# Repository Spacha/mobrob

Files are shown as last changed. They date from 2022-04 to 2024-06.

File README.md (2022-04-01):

# mobrob

A mobile robot 

## Features

* Obstacle detection and avoidance
* Room mapping (explore mode?)
* Manual control (throttle + steer)
  * For example, through browser-based GUI
* Automatic navigation (A to B) (after exploring space?)
  * Complete more complex tasks like _fetch an item_?
* Charging capability preferable (e.g. MCP73831)
  * https://www.youtube.com/watch?v=GRd9uTwg7r4&ab_channel=MicroTypeEngineering
  * https://www.youtube.com/watch?v=TyaW8ZKumno&ab_channel=PlumPot

# Initial design

Datasheets for components are found in `Datasheets` folder.

* **Processor & connectivity**: ESP8266 | [datasheet](datasheets/ESP8266EX_datasheet-v4.4.pdf)
  * These values are for ESP8266EX
  * WiFi: 802.11 b/g/n Wifi, 2.4-2.5 GHz
  * Peripherals: UART / SDIO / SPI / I2C / I2S / IR Remote Control / GPIO / PWM
  * Operating voltage 3.3V (3.0-3.6V)
  * Average operating current: 80 mA
  * Around 50 kB RAM (for user, when connected to a station)
  * **Requires external SPI flash!** Up to 16 MB flash can be supported
    * Suggested: 512 kB (without OTA), 1 MB (with OTA)
  * Single core, 80 MHz
* **Dual H-bridge motor driver**: L293D | [datasheet](datasheets/L293x_datasheet.pdf)
* Power management:
  * **Battery**: 11.1V Li-Po (6-12V), (3 x 3.7V cells)
    * Price: $20-40
  * **Buck converter (12V->5V)**: LM2596 or other...
    * https://www.youtube.com/watch?v=C7-8nUU6e3E&t=2367s
  * **LDO (5V->3.3V)**: LM7805
    * https://electronics.stackexchange.com/questions/420999/use-5v-linear-regulator-and-ldo-3-3v

* **Motors & chassis**: Dual motor tank chassis (3-7V)
  * https://www.aliexpress.com/item/4000115994387.html?spm=a2g0o.order_list.0.0.21ef1802jPbMxm
  * Has slot for 4xAA batteries, could be modified to fit the rechargable 3-cell Li-Po battery.
  * Size: 9.7cm x 18.5cm x 5cm (width x length x height )
  * Motors: 130 size generic, can be replaced if necessary
  * Price: $18.50

* Sensors (both for proximity and distance, and other):
  * IMU?
  * UT/IR?
  * Others?

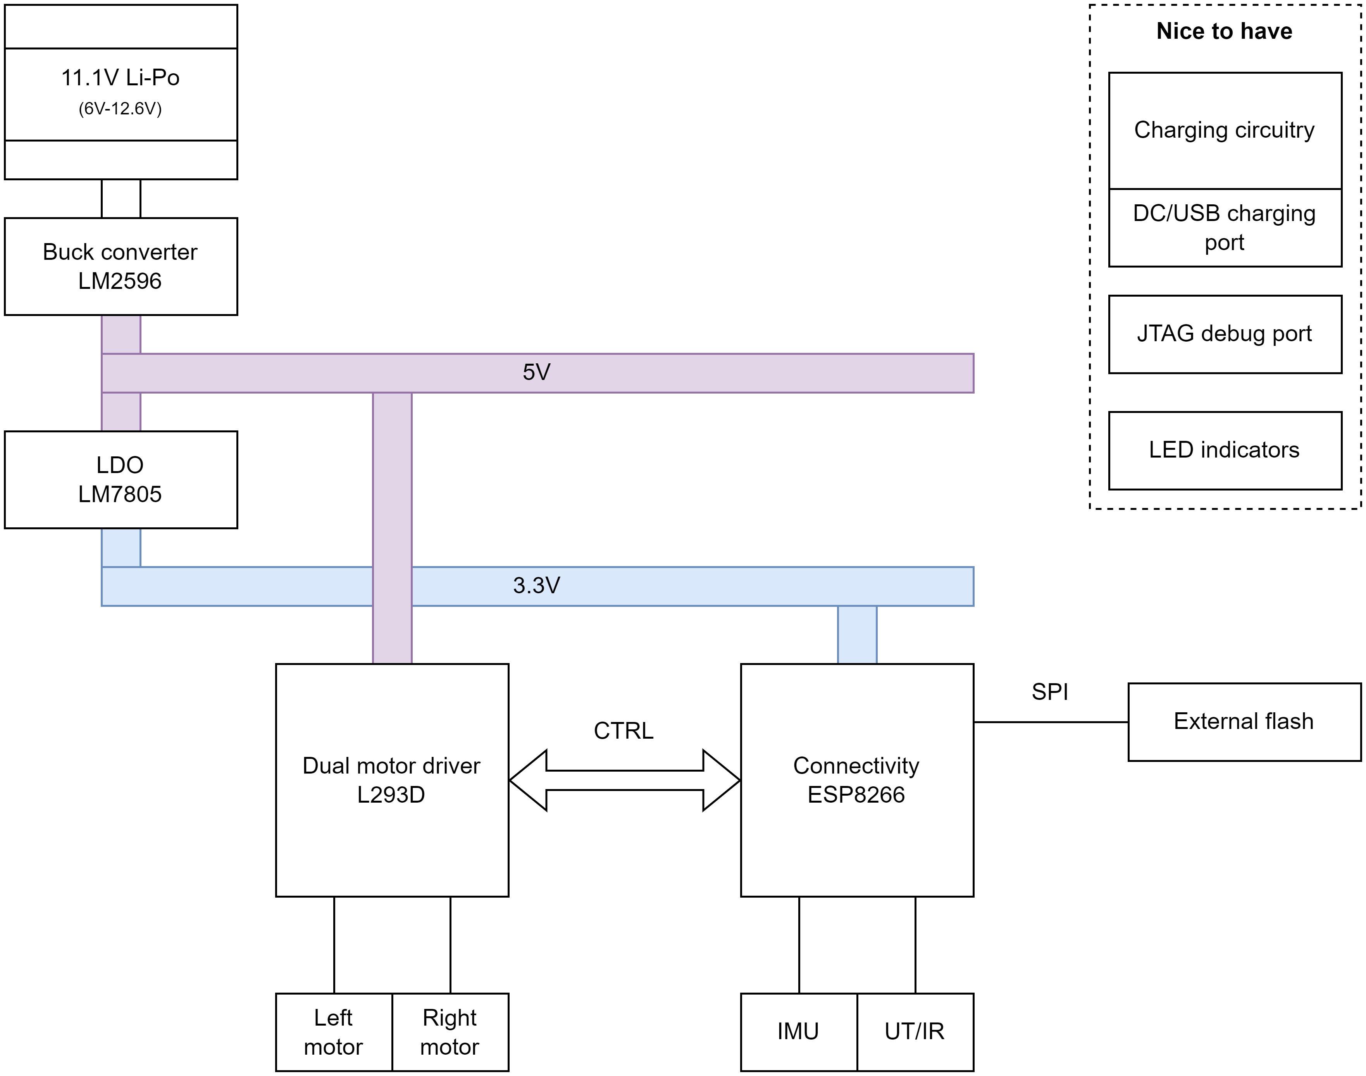
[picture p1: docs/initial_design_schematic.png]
Initial design.


# Discussion

I am not sure if either ESP32 or ESP8266 come in QFP format (only in QFN, no-leads). I guess JLCPCB and others also assemble these devices so maybe this is not an issue.

## ESP32
ESP32 would be considerably better than ESP8266. It has a lot more functionality and also has 8MB of onboard flash (ESP32-S3FN8, see ESP32-S3 datasheet, p.11).

* https://www.youtube.com/watch?v=WWIy6a0T7WM&ab_channel=PlumPot
* Decoupling caps (as close of the pins as possible)
* External crystal? (see Phil's lab)
* Note the antenna/RF part!
  * No traces (or any copper) beneath the antenna part!
* Careful with differential pairs

* https://en.wikipedia.org/wiki/ESP32#ESP32-S3:
  * ESP32-WROOM-32D: PCB trace antenna, 4 MiB flash (probably preferable)
  * ESP32-WROOM-32U: U.FL socket antenna, 4 MiB flash

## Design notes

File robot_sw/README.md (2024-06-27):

# Mobrob

In this project, a mobile robot with remote control capability is developed. The robot will be able to wirelessly connect to Wi-Fi and sense the obstacles in its environment. The robot will be able to receive commands from the remote server, and send sensor readings and other data back to the server.

The system can be used as a base for a robot-based home security system, an in-home sensor platform, or with some improvements, even for industrial applications, completing dull, dirty, and dangerous tasks.

Miika and Essi

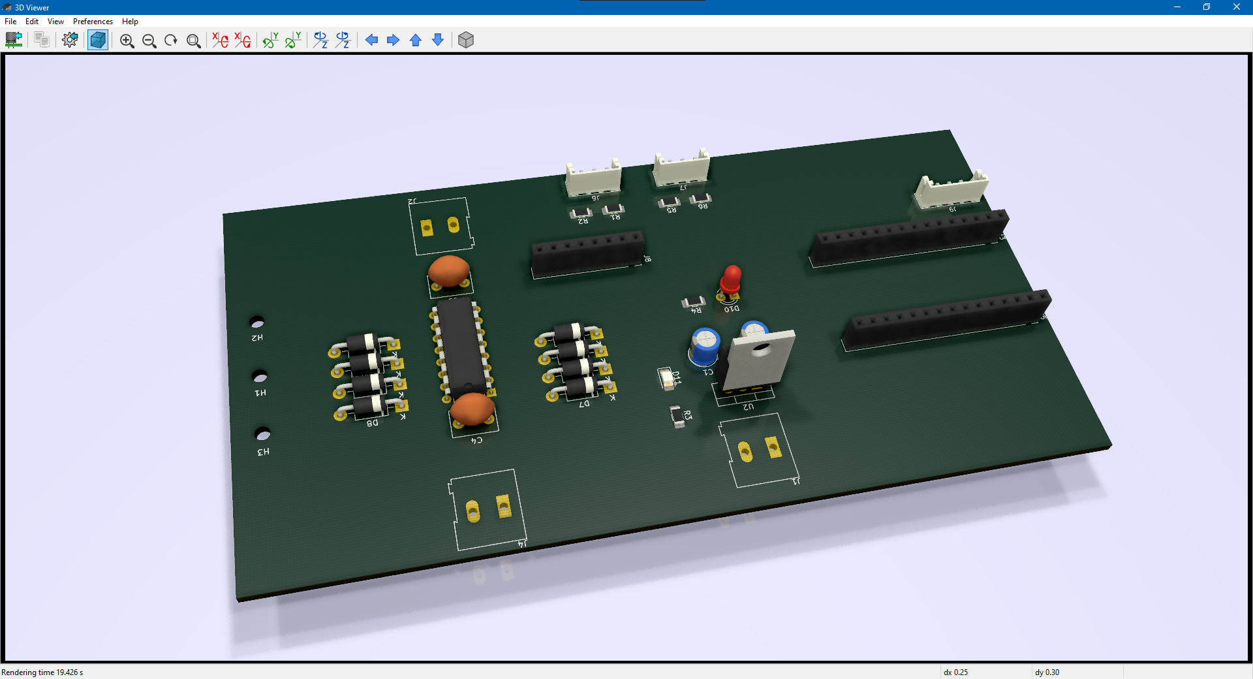
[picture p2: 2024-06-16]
Annotation 2024-05-02 180300.png

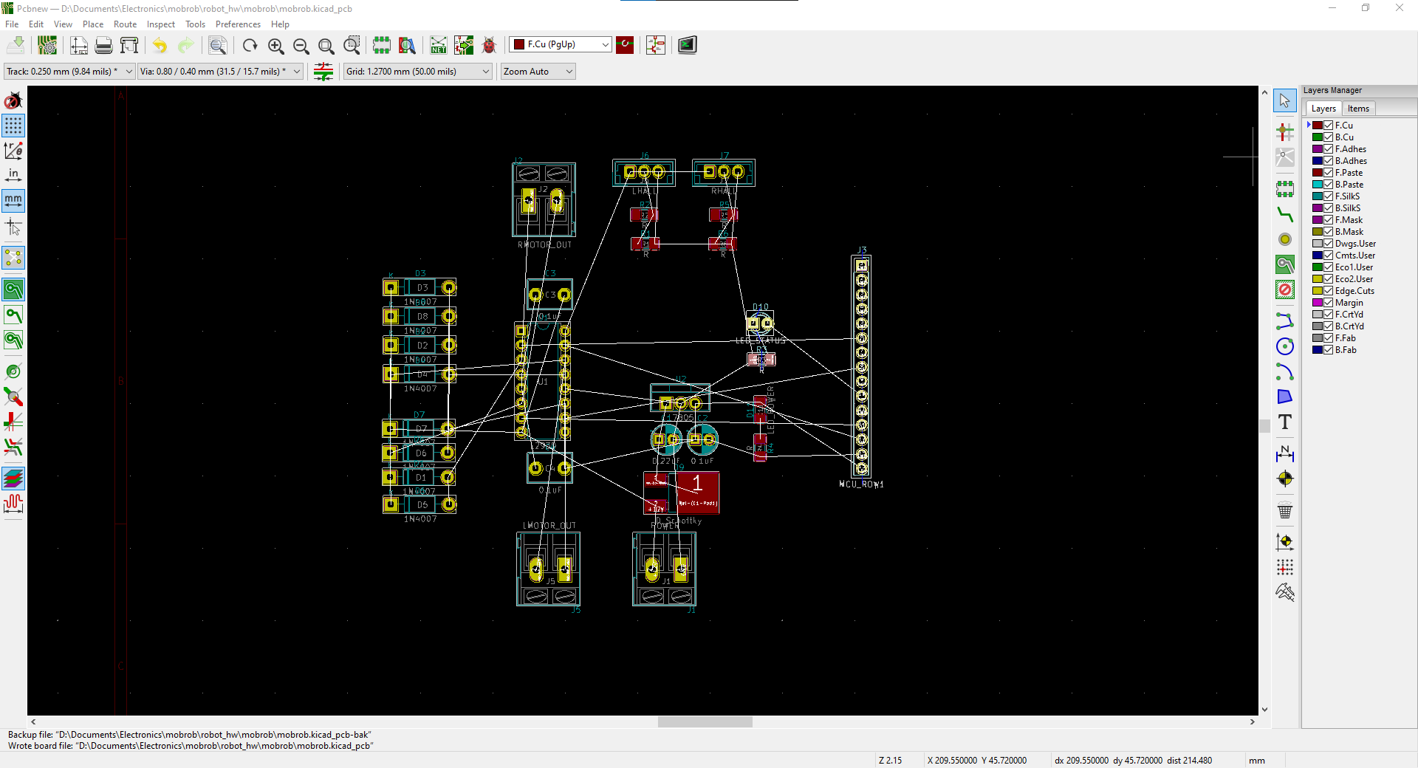
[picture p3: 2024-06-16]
Annotation 2024-04-15 024806.png

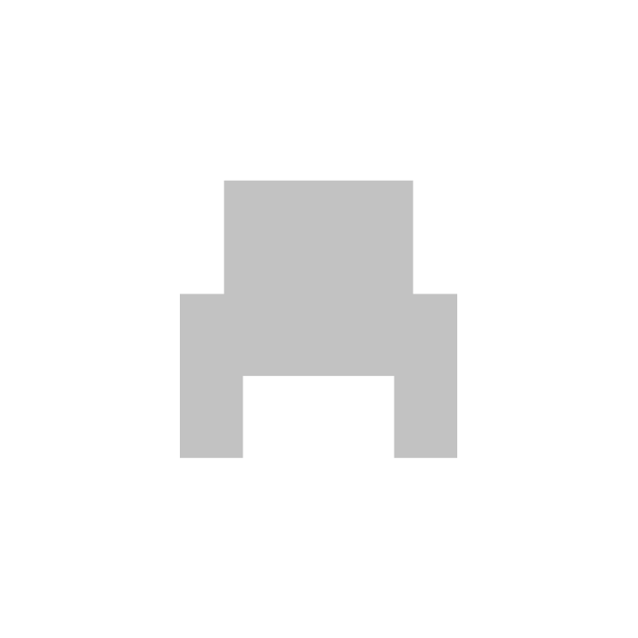
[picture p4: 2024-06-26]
server_sw/resources/view_rear.png

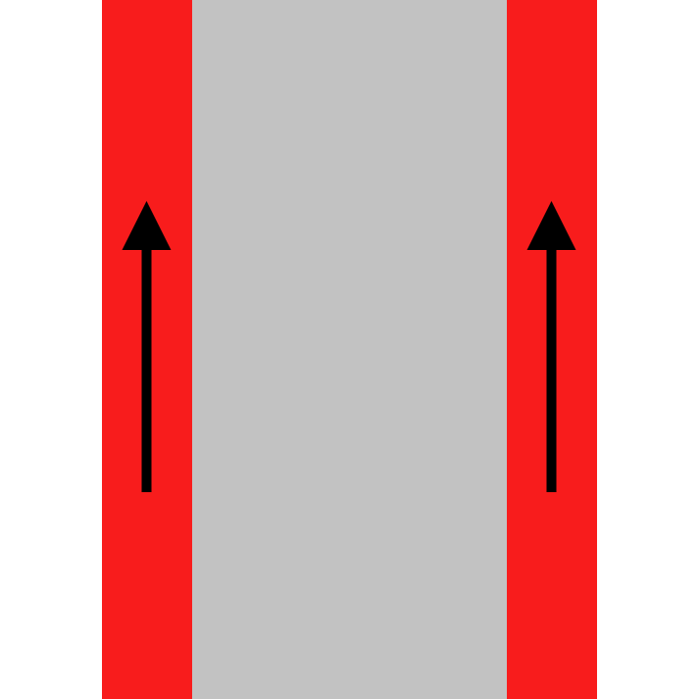
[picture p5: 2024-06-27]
server_sw/resources/view_top_lfrf.png

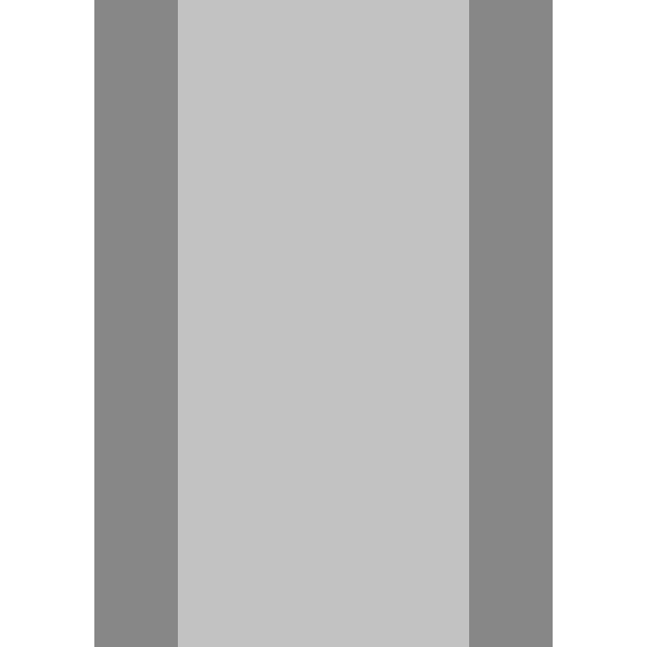
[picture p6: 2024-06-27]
server_sw/resources/view_top.png

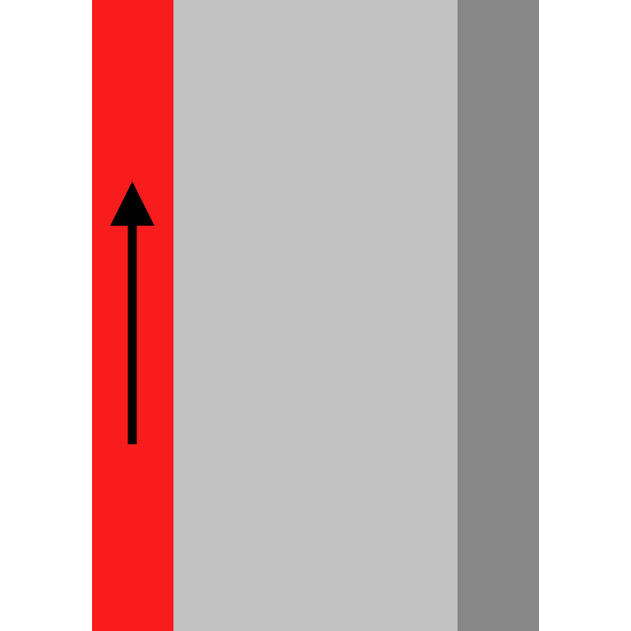
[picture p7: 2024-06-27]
server_sw/resources/view_top_lf.png

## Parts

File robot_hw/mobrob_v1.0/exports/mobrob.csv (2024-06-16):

Reference | Value | Datasheet | Footprint | Qty | DNP
C1 | 0.22uF | ~ | Capacitor_THT:CP_Radial_D10.0mm_P5.00mm | 1
C2,C3,C4 | 0.1uF | ~ | -- mixed values -- | 3
D1,D2,D3,D4,D5,D6,D7,D8 | M7 | https://diotec.com/request/datasheet/m1.pdf | Diode_SMD:D_SMA_Handsoldering | 8
D9 | LED_STATUS | http://cdn-reichelt.de/documents/datenblatt/A500/LL-504BC2E-009.pdf | LED_THT:LED_D5.0mm | 1
D10 | LED_POWER | https://optoelectronics.liteon.com/upload/download/DS-22-98-0004/LTST-C150GKT.pdf | LED_SMD:LED_1206_3216Metric_Pad1.42x1.75mm_HandSolder | 1
J1 | RMOTOR | https://www.on-shore.com/wp-content/uploads/ED555XDS.pdf | TerminalBlock_Phoenix:TerminalBlock_Phoenix_PT-1,5-2-3.5-H_1x02_P3.50mm_Horizontal | 1
J2 | LMOTOR | https://www.on-shore.com/wp-content/uploads/ED555XDS.pdf | TerminalBlock_Phoenix:TerminalBlock_Phoenix_PT-1,5-2-3.5-H_1x02_P3.50mm_Horizontal | 1
J3 | POWER | https://www.on-shore.com/wp-content/uploads/ED555XDS.pdf | TerminalBlock_Phoenix:TerminalBlock_Phoenix_PT-1,5-2-3.5-H_1x02_P3.50mm_Horizontal | 1
J4 | ESP32_1 | ~ | Connector_PinSocket_2.54mm:PinSocket_1x15_P2.54mm_Vertical | 1
J5 | ESP32_2 | ~ | Connector_PinSocket_2.54mm:PinSocket_1x15_P2.54mm_Vertical | 1
J6,J7 | LHALL | ~ | Connector_PinHeader_2.54mm:PinHeader_1x03_P2.54mm_Vertical | 2
J8 | IMU | ~ | Connector_PinSocket_2.54mm:PinSocket_1x08_P2.54mm_Vertical | 1
J9 | UT | ~ | Connector_PinHeader_2.54mm:PinHeader_1x04_P2.54mm_Vertical | 1
R1,R2 | 150 | ~ | Resistor_SMD:R_0805_2012Metric_Pad1.20x1.40mm_HandSolder | 2
U1 | L293D | http://www.ti.com/lit/ds/symlink/l293.pdf | Package_DIP:DIP-16_W7.62mm | 1
U2 | L7805 | http://www.st.com/content/ccc/resource/technical/document/datasheet/41/4f/b3/b0/12/d4/47/88/CD00000444.pdf/files/CD00000444.pdf/jcr:content/translations/en.CD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 | Package_TO_SOT_THT:TO-220-3_Vertical | 1

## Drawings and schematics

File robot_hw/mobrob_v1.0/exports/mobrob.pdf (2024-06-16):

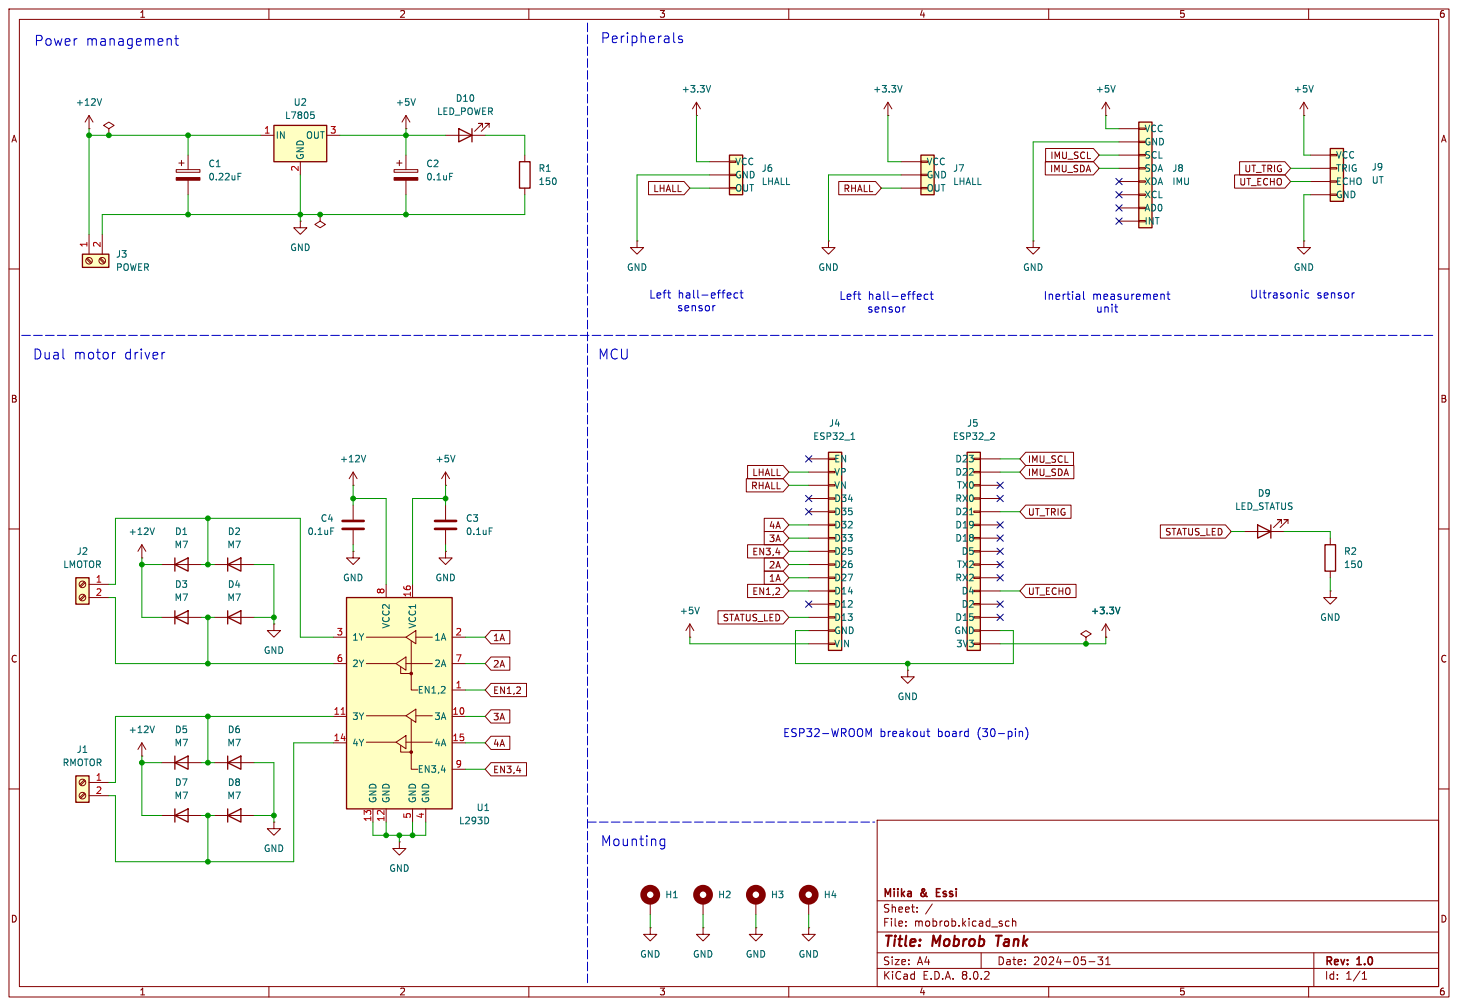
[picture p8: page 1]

Left hall-effect sensor ESP32-WROOM breakout board (30-pin)

Id: 1/1 Title: Mobrob Tank

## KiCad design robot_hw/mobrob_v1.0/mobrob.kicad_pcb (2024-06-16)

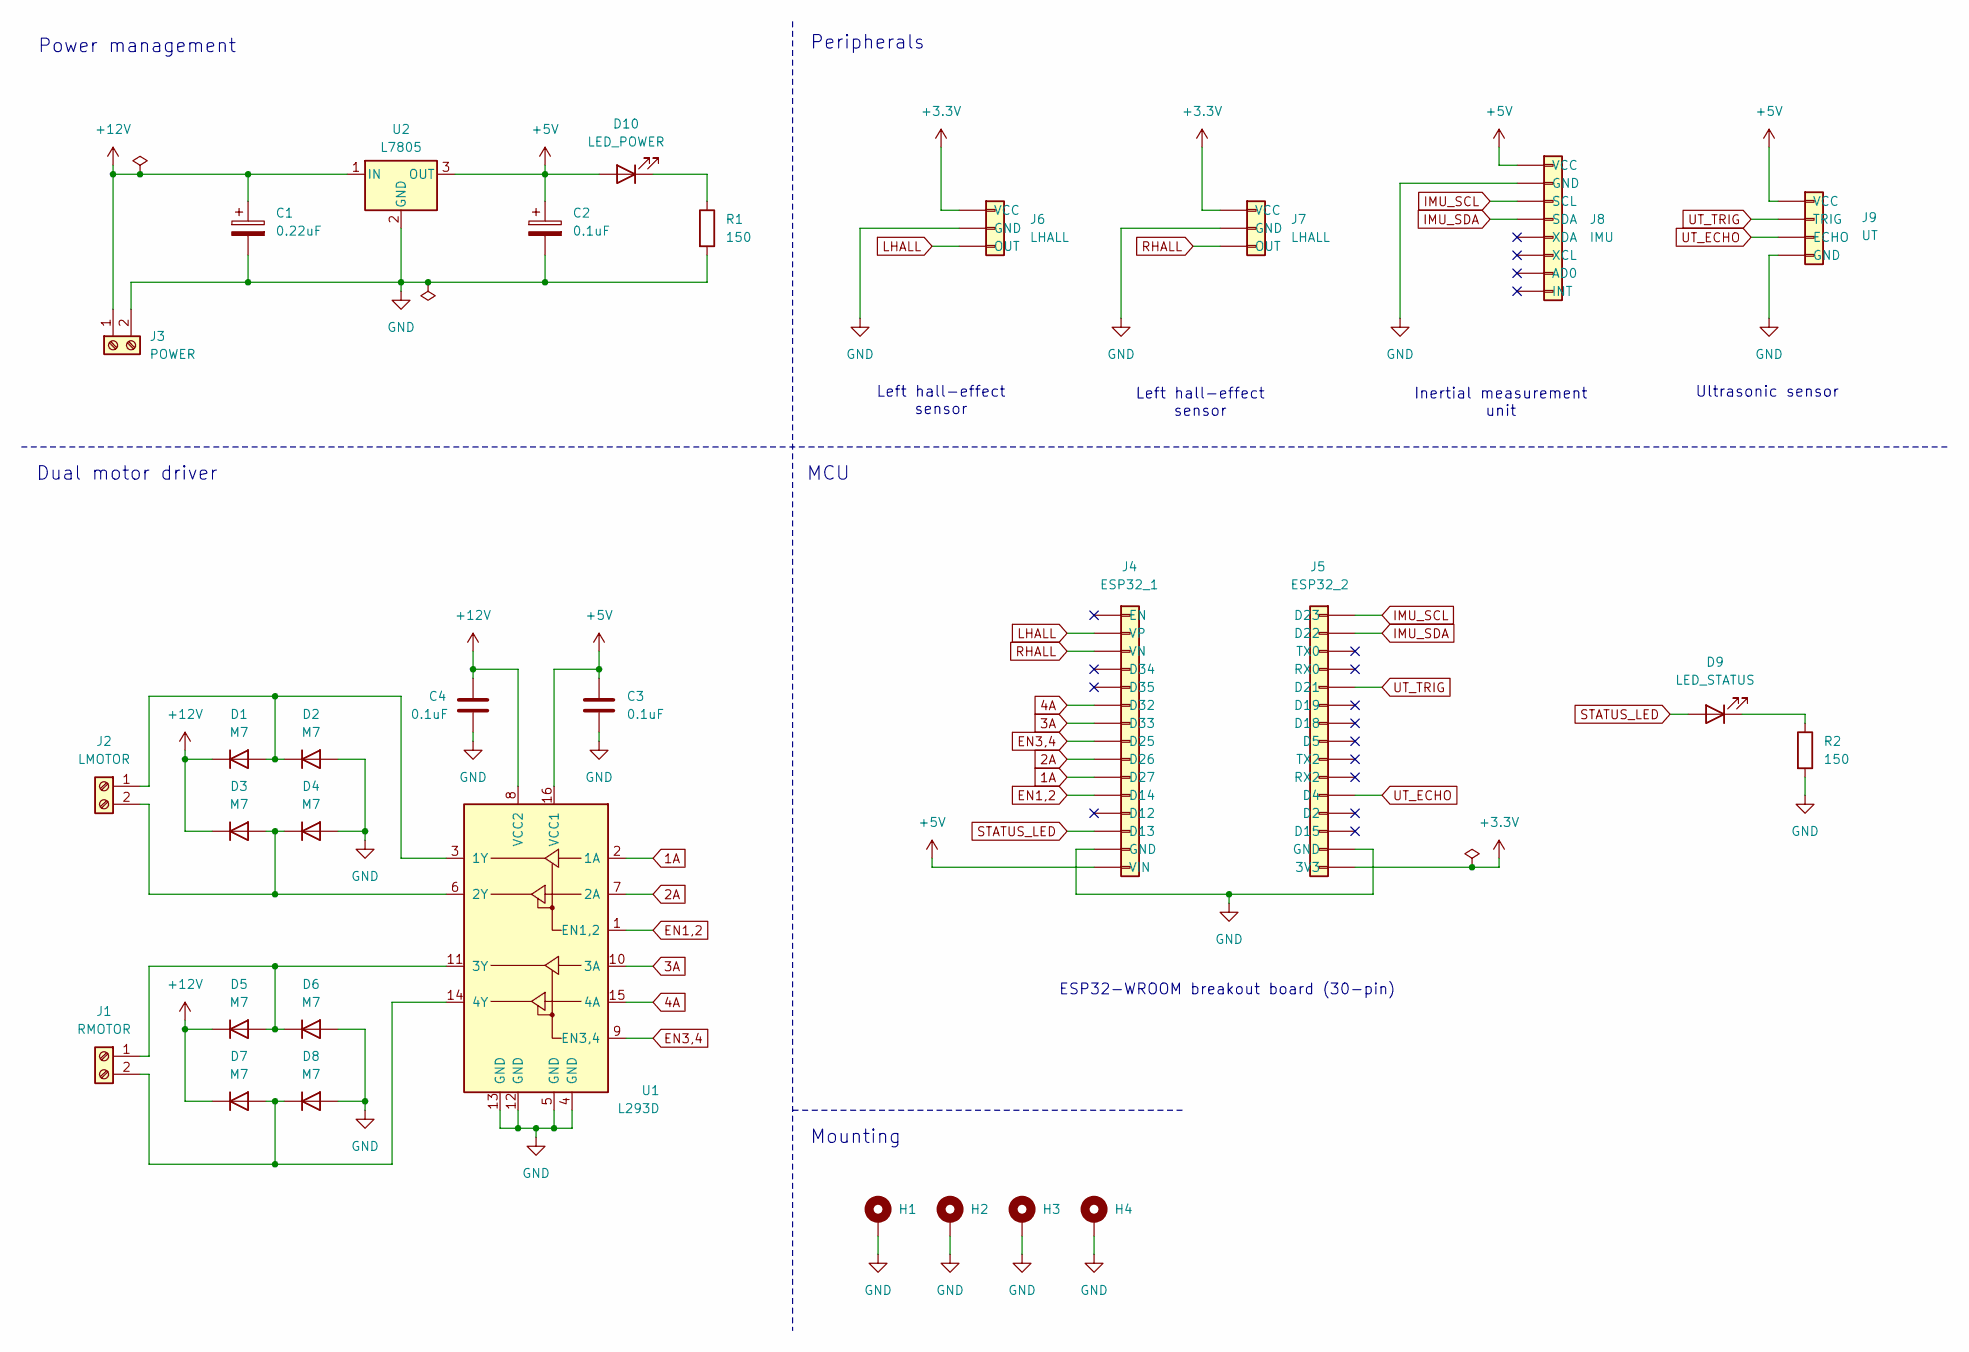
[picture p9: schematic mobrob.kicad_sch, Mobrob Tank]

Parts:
C1: 0.22uF; CP_Radial_D10.0mm_P5.00mm
C2: 0.1uF; CP_Radial_D10.0mm_P5.00mm
C3, C4: 0.1uF; C_1206_3216Metric_Pad1.33x1.80mm_HandSolder
D1, D2, D3, D4, D5, D6, D7, D8: M7; D_SMA_Handsoldering
D9: LED_STATUS; LED_D5.0mm
D10: LED_POWER; LED_1206_3216Metric_Pad1.42x1.75mm_HandSolder
H1, H2, H3, H4: MountingHole_Pad; MountingHole_3.2mm_M3_Pad_Via
J1: RMOTOR; TerminalBlock_Phoenix_PT-1,5-2-3.5-H_1x02_P3.50mm_Horizontal
J2: LMOTOR; TerminalBlock_Phoenix_PT-1,5-2-3.5-H_1x02_P3.50mm_Horizontal
J3: POWER; TerminalBlock_Phoenix_PT-1,5-2-3.5-H_1x02_P3.50mm_Horizontal
J4: ESP32_1; PinSocket_1x15_P2.54mm_Vertical
J5: ESP32_2; PinSocket_1x15_P2.54mm_Vertical
J6, J7: LHALL; PinHeader_1x03_P2.54mm_Vertical
J8: IMU; PinSocket_1x08_P2.54mm_Vertical
J9: UT; PinHeader_1x04_P2.54mm_Vertical
R1, R2: 150; R_0805_2012Metric_Pad1.20x1.40mm_HandSolder
U1: L293D; DIP-16_W7.62mm
U2: L7805; TO-220-3_Vertical

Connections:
1A: J4.10 (D27), U1.2 (1A)
2A: J4.9 (D26), U1.7 (2A)
3A: J4.7 (D33), U1.10 (3A)
4A: J4.6 (D32), U1.15 (4A)
+3.3V: J5.15 (3V3), J6.1 (VCC), J7.1 (VCC)
+5V: C2.1, C3.1, D10.2 (A), J4.15 (VIN), J8.1 (VCC), J9.1 (VCC), U1.16 (VCC1), U2.3 (OUT)
+12V: C1.1, C4.1, D1.1 (K), D3.1 (K), D5.1 (K), D7.1 (K), J3.1, U1.8 (VCC2), U2.1 (IN)
EN1,2: J4.11 (D14), U1.1 (EN1,2)
EN3,4: J4.8 (D25), U1.9 (EN3,4)
GND: C1.2, C2.2, C3.2, C4.2, D2.2 (A), D4.2 (A), D6.2 (A), D8.2 (A), H1.1, H2.1, H3.1, H4.1, J3.2, J4.14 (GND), J5.14 (GND), J6.2 (GND), J7.2 (GND), J8.2 (GND), J9.4 (GND), R1.2, R2.2, U1.4 (GND), U1.5 (GND), U1.12 (GND), U1.13 (GND), U2.2 (GND)
IMU_SCL: J5.1 (D23), J8.3 (SCL)
IMU_SDA: J5.2 (D22), J8.4 (SDA)
LHALL: J4.2 (VP), J6.3 (OUT)
unnamed: D1.2 (A), D2.1 (K), J2.1, U1.3 (1Y)
unnamed: D3.2 (A), D4.1 (K), J2.2, U1.6 (2Y)
unnamed: D5.2 (A), D6.1 (K), J1.1, U1.11 (3Y)
unnamed: D7.2 (A), D8.1 (K), J1.2, U1.14 (4Y)
unnamed: D9.1 (K), R2.1
unnamed: D10.1 (K), R1.1
RHALL: J4.3 (VN), J7.3 (OUT)
STATUS_LED: D9.2 (A), J4.13 (D13)
UT_ECHO: J5.11 (D4), J9.3 (ECHO)
UT_TRIG: J5.5 (D21), J9.2 (TRIG)

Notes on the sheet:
Power management
Dual motor driver
MCU
Left hall-effect sensor
Mounting
ESP32-WROOM breakout board (30-pin)
Inertial measurement unit
Peripherals
Ultrasonic sensor

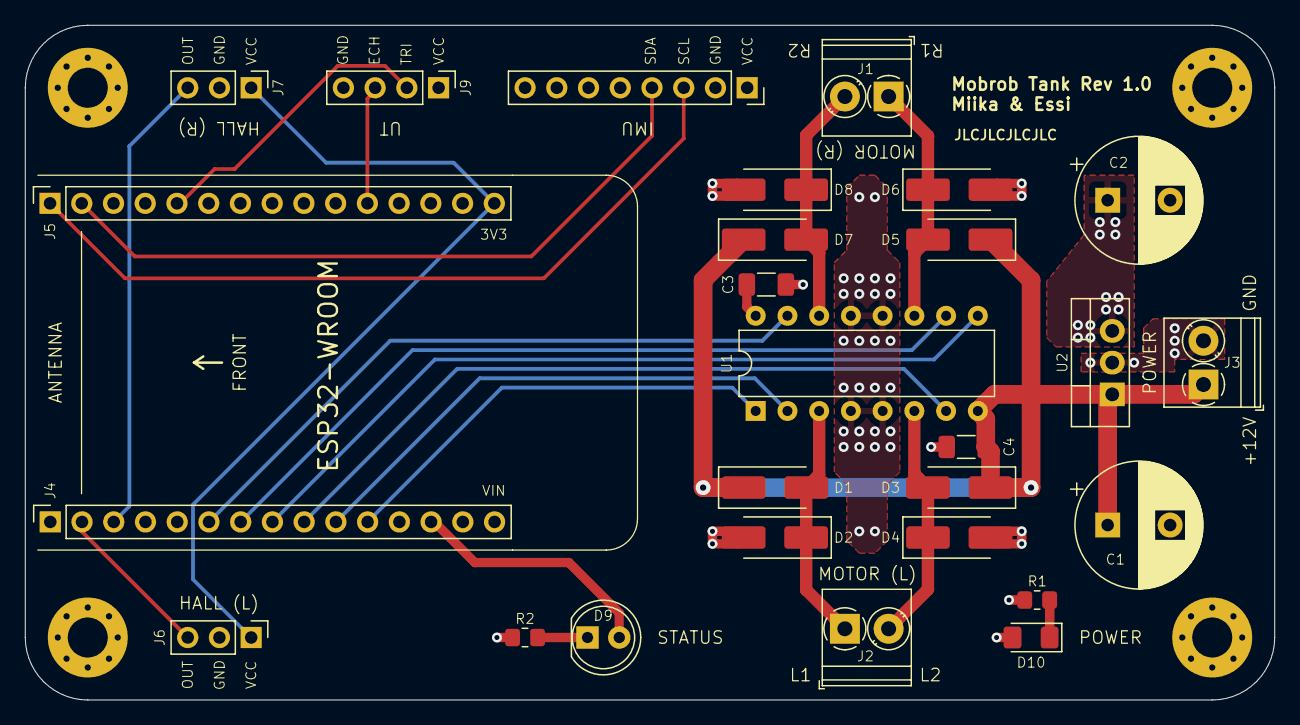
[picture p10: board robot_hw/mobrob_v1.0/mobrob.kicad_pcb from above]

Board: 4 copper layers, 100.0 x 54.0 mm, 31 parts (0 on the bottom side), 23 nets.

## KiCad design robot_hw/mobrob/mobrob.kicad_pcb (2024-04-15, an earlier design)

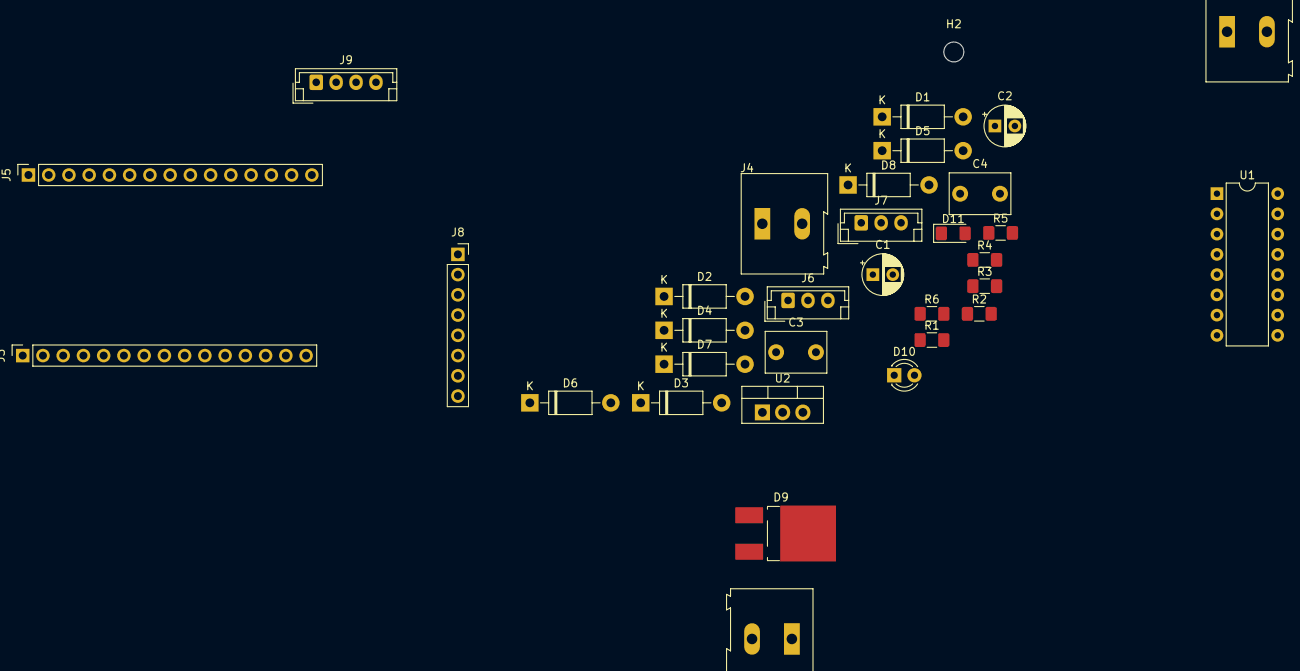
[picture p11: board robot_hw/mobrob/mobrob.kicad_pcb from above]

Board: 2 copper layers, 35 parts (0 on the bottom side), 24 nets, no tracks yet.

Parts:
C1: 0.22uF; CP_Radial_D5.0mm_P2.50mm
C2: 0.1uF; CP_Radial_D5.0mm_P2.50mm
C3, C4: 0.1uF; C_Disc_D7.5mm_W5.0mm_P5.00mm
D1, D2, D3, D4, D5, D6, D7, D8: 1N4007; D_DO-41_SOD81_P10.16mm_Horizontal
D9: D_Schottky; TO-252-2_TabPin1
D10: LED_STATUS; LED_D3.0mm
D11: LED_POWER; LED_1206_3216Metric_Pad1.42x1.75mm_HandSolder
H1, H2, H3: MountingHole; MountingHole_2.5mm
J1: POWER; TerminalBlock_Altech_AK300-2_P5.00mm
J2, J4: RMOTOR_OUT; TerminalBlock_Altech_AK300-2_P5.00mm
J3: MCU_ROW1; PinSocket_1x15_P2.54mm_Vertical
J5: MCU_ROW2; PinSocket_1x15_P2.54mm_Vertical
J6: LHALL; JST_EH_B3B-EH-A_1x03_P2.50mm_Vertical
J7: RHALL; JST_EH_B3B-EH-A_1x03_P2.50mm_Vertical
J8: IMU; PinSocket_1x08_P2.54mm_Vertical
J9: UT; JST_EH_B4B-EH-A_1x04_P2.50mm_Vertical
R1, R2, R3, R4, R5, R6: R; R_1206_3216Metric_Pad1.42x1.75mm_HandSolder
U1: L293D; DIP-16_W7.62mm
U2: L7805; TO-220-3_Vertical

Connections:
1A: J3.6, U1.2
2A: J3.12, U1.7
3A: J3.8, U1.10
4A: J3.13, U1.15
+5V: C2.1, C4.2, D11.2, J3.15, J6.1, J7.1, J8.1, J9.1, U1.16, U2.3
+12V: D1.1, D2.1, D3.1, D4.1, D9.2, J1.2
GND: C1.2, C2.2, C3.1, C4.1, D5.2, D6.2, D7.2, D8.2, J1.1, J3.14, J5.14, J6.3, J7.3, J8.2, J9.4, R1.2, R3.1, R4.2, R6.2, U1.4, U1.5, U1.12, U1.13, U2.2
IMU_SCL: J5.2, J8.3
IMU_SDA: J5.5, J8.4
LED_STATUS: D10.2, J3.10
LHALL_IN: J3.3, R2.1
unnamed: C1.1, D9.1, U2.1
unnamed: C3.2, U1.8
unnamed: D1.2, D5.1, J2.1, U1.3
unnamed: D2.2, D6.1, J2.2, U1.6
unnamed: D3.2, D7.1, J4.1, U1.11
unnamed: D4.2, D8.1, J4.2, U1.14
unnamed: D10.1, R3.2
unnamed: D11.1, R4.1
unnamed: J6.2, R1.1, R2.2
unnamed: J7.2, R5.2, R6.1
RHALL_IN: J3.2, R5.1
UT_ECHO: J5.1, J9.3
UT_TRIG: J5.11, J9.2

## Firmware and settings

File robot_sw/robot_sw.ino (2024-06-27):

/*
 * This file is part of the Mobrob project.
 *
 * This is the main entrypoint of the robot software.
 *
 * Miika & Essi
 */

#include "mobrob.h"
#include "Drive.h"
#include "MobrobClient.h"
#include "sensors/UltrasonicSensor.h"
#include "sensors/IMUSensor.h"

///////////////////////////////////////
// Set up modules
///////////////////////////////////////

Drive drive(PIN_L1, PIN_L2, PIN_LEN,
            PIN_R1, PIN_R2, PIN_REN);

MobrobClient client(IPAddress(SERVER_ADDR), SERVER_PORT,
                    update_configuration, control);

UltrasonicSensor ut_sensor(PIN_UT_TRIG, PIN_UT_ECHO);

IMUSensor imu_sensor(PIN_IMU_SDA, PIN_IMU_SCL);

///////////////////////////////////////
// Configuration
///////////////////////////////////////

Status g_status = UNCONNECTED;
Mode g_mode = MANUAL;

float g_track_speed = 0.0;
float g_left_track_speed = 0.0;
float g_right_track_speed = 0.0;

// TODO: An update struct?
float g_roll = 0.0;
float g_pitch = 0.0;
float g_temperature = 0.0;
float g_travel_dist = 0.0;
float g_obstacle_dist = 999.9;


void setup()
{
  Wire.setPins(PIN_IMU_SDA, PIN_IMU_SCL);

  Serial.begin(115200);
  delay(100);

  client.setup();
  if (!imu_sensor.setup())
    PRINTLN("Error: failed to initiate IMU sensor!");

  ///////////////////////////////////////
  // Set up pins
  ///////////////////////////////////////

  pinMode(PIN_STATUS_LED, OUTPUT);
  pinMode(PIN_UT_TRIG, OUTPUT);
  pinMode(PIN_UT_ECHO, INPUT);
  pinMode(PIN_LEN, OUTPUT);
  pinMode(PIN_L1, OUTPUT);
  pinMode(PIN_L2, OUTPUT);
  pinMode(PIN_REN, OUTPUT);
  pinMode(PIN_R1, OUTPUT);
  pinMode(PIN_R2, OUTPUT);

  PRINTLN("Initialized. Commands:");
  PRINTLN("1. drive <left_direction> <right_direction>");
  PRINTLN("2. brake <1 (apply) | 0 (release)>");
  PRINTLN("3. speed <speed>");
  PRINTLN("4. status <0 (UNCONNECTED) | 1 (CONNECTED)>");
  PRINTLN();

  drive.control(0.0, 0.0);

  ///////////////////////////////////////
  // Start tasks
  ///////////////////////////////////////

  xTaskCreate(TaskControl,            "Control",            2048, NULL, 1, NULL);
  xTaskCreate(TaskMaintainConnection, "MaintainConnection", 4096, NULL, 2, NULL);
  xTaskCreate(TaskSendUpdate,         "SendUpdate",         4096, NULL, 3, NULL);
  xTaskCreate(TaskReceiveSerial,      "ReceiveSerial",      2048, NULL, 4, NULL);
  xTaskCreate(TaskBlink,              "Blink",              2048, NULL, 5, NULL);
}

void loop() { /* Not used with FreeRTOS */ }

///////////////////////////////////////////////////////////////////////////////
// Task definitions
///////////////////////////////////////////////////////////////////////////////

/**
 * Task for controlling the robot's movement in 'real-time',
 * based on the current control commands.
 *
 * @param params No parameters used.
 */
void TaskControl(void *params)
{
  (void)params;

  //long started_turning_at = -1;
  bool turning = false;

  for (;;) {
    // TODO: hall measurements - move from the old FW version

    // if connected and in the EXPLORE mode,
    // drive avoiding obstacles by turning
    if (g_status == CONNECTED && g_mode == EXPLORE)
    {
      if (turning)
      {
        if (g_obstacle_dist > 30.0)
        {
          PRINTLN("[EXP] Stop turning");
          g_left_track_speed = 0;
          g_right_track_speed = 0;
          turning = false;
        }
      }

      if (!turning)
      {
        // start turning
        if (g_obstacle_dist <= 15.0)
        {
          PRINTLN("[EXP] Start turning");
          g_left_track_speed = g_track_speed;
          g_right_track_speed = -g_track_speed;
          turning = true;
        }
        // drive forward
        else
        {
          g_left_track_speed = g_track_speed;
          g_right_track_speed = g_track_speed;
        }
      }
    }

    drive.control(g_left_track_speed, g_right_track_speed);
    vTaskDelay(25 / portTICK_PERIOD_MS);
  }
}

/**
 * Task for receiving commands from the serial port when in debug mode.
 *
 * @param params No parameters used.
 */
void TaskReceiveSerial(void *params)
{
  (void)params;

  for (;;)
  {
    if (Serial.available() > 0)
    {
      String input = Serial.readStringUntil('\n');
      input.trim();

      if (input.startsWith("brake "))
      {
        int brakeValue = input.substring(6).toInt();
        if (brakeValue == 1)
        {
          drive.apply_brake();
          PRINTLN("Brake applied");
        }
        else if (brakeValue == 0)
        {
          drive.release_brake();
          PRINTLN("Brake released");
        }
        else
        {
          PRINTLN("Invalid brake command. Use: brake <1 (apply) | 0 (release)>");
        }
      }
      else if (input.startsWith("status "))
      {
        int statusValue = input.substring(7).toInt();
        if (statusValue == 1)
        {
          g_status = CONNECTED;
          PRINTLN("Status set to CONNECTED");
        }
        else if (statusValue == 0)
        {
          g_status = UNCONNECTED;
          PRINTLN("Status set to UNCONNECTED");
        }
        else
        {
          PRINTLN("Invalid status command. Use: status <0 (UNCONNECTED) | 1 (CONNECTED)>");
        }
      }
      else if (input.startsWith("drive "))
      {
        float left_speed = 0.0;
        float right_speed = 0.0;

        int spaceIndex = input.indexOf(' ', 6);
        if (spaceIndex > 0)
        {
          String leftSpeedStr = input.substring(6, spaceIndex);
          String rightSpeedStr = input.substring(spaceIndex + 1);

          left_speed = leftSpeedStr.toFloat();
          right_speed = rightSpeedStr.toFloat();

          g_left_track_speed = g_track_speed * left_speed;
          g_right_track_speed = g_track_speed * right_speed;

          PRINT("Left speed: ");
          PRINT(left_speed);
          PRINT(", Right speed: ");
          PRINTLN(right_speed);
        }
        else
        {
          PRINTLN("Invalid input format. Use: <left_speed> <right_speed>");
        }
      }
      else if (input.startsWith("speed "))
      {
        int speed = input.substring(6).toFloat();

        g_track_speed = speed;

        PRINT("Speed set to ");
        PRINTLN(speed);
      }
      else
      {
        PRINTLN("Invalid command.");
      }
    }

    vTaskDelay(100 / portTICK_PERIOD_MS);
  }
}

/**
 * Task for blinking the status LED.
 *
 * @param params No parameters used.
 */
void TaskBlink(void *params)
{
  (void)params;

  const int delay_unconnected = 250;
  const int delay_connected   = 1000;

  for (;;) {
    digitalWrite(PIN_STATUS_LED, HIGH);
    if (g_status == CONNECTED)
      vTaskDelay(delay_connected / portTICK_PERIOD_MS);
    else
      vTaskDelay(delay_unconnected / portTICK_PERIOD_MS);

    digitalWrite(PIN_STATUS_LED, LOW);
    if (g_status == CONNECTED)
      vTaskDelay(delay_connected / portTICK_PERIOD_MS);
    else
      vTaskDelay(delay_unconnected / portTICK_PERIOD_MS);
  }
}

/**
 * Task for sending data updates to the server.
 *
 * @param params No parameters used.
 */
void TaskSendUpdate(void *params)
{
  (void)params;

  const int update_rate = 250;

  imu_data_t imu_data;

  for (;;)
  {
    // if connected, take a measurement and send an update to the server
    if (g_status == CONNECTED)
    {
      imu_sensor.measure_all(&imu_data);
      g_roll = imu_data.roll;
      g_pitch = imu_data.pitch;
      g_temperature = imu_data.temperature;

      //g_travel_dist = g_travel_dist + (float)random(0, 5) / 10;
      g_obstacle_dist = ut_sensor.measure_distance();

      client.send_robot_update(g_roll, g_pitch, g_temperature, g_travel_dist, g_obstacle_dist);
    }

    vTaskDelay(update_rate / portTICK_PERIOD_MS);
  }
}

/**
 * Task for maintaining the robot's connection with the server.
 *
 * @param params No parameters used.
 */
void TaskMaintainConnection(void *params)
{
  (void)params;

  const int wifi_poll_delay     = 5000;
  const int wifi_timeout        = 20000;
  const int wifi_recover_delay  = 15000;

  for (;;)
  {
    // connected: sleep for a while and then check again
    if (client.connected())
    {
      vTaskDelay(wifi_poll_delay / portTICK_PERIOD_MS);
      continue;
    }

    // unconnected: try connecting
    g_status = UNCONNECTED;
    drive.control(0.0, 0.0);
    
    if (client.try_connect(wifi_timeout))
    {
      // just connected
      g_status = CONNECTED;
      continue;
    }

    // connection failed: sleep for a while and try again
    PRINTLN("[CLIENT] Error: Connection failed.");
    vTaskDelay(wifi_recover_delay / portTICK_PERIOD_MS);
  }
}

/**
 * Update the robot's configuration.
 *
 * @param track_speed The track speed of both tracks [0, 1]
 * @param mode The robot's mode {MANUAL, EXPLORE}
 */
void update_configuration(float track_speed, Mode mode)
{
  // Update the configuration based on the received values
  PRINT("Track Speed: ");
  PRINTLN(track_speed);
  PRINT("Mode: ");
  PRINTLN(mode == MANUAL ? "MANUAL" : "EXPLORE");

  if (g_mode == EXPLORE && mode == MANUAL)
  {
    g_left_track_speed = 0;
    g_right_track_speed = 0;
  }

  g_track_speed = track_speed;
  g_mode = mode;
}

/**
 * Control the robot's driving.
 *
 * @param left_track The direction of the left track {-1, 0, 1}
 * @param right_track The direction of the right track {-1, 0, 1}
 */
void control(float left_track, float right_track)
{
  g_left_track_speed = left_track * g_track_speed;
  g_right_track_speed = right_track * g_track_speed;
}

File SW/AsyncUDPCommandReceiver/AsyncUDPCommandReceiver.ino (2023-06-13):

//#include <Ticker.h>
#include "WiFi.h"
#include "AsyncUDP.h"
#include "network_credentials.h"

// Pin assignments

#define BLINKER_PIN 27  // LED

#define LHALL_PIN 35    // Left track hall sensor
#define RHALL_PIN 34    // Right track hall sensor

#define UT_TRIG_PIN 4   // Ultrasonic sensor trigger
#define UT_ECHO_PIN 23  // Ultrasonic sensor echo

#define L1_PIN      25  // Left motor control 1
#define L2_PIN      13  // Left motor control 2
#define LEN_PIN     26  // Left motor enable
#define R1_PIN      32  // Right motor control 1
#define R2_PIN      12  // Right motor control 2
#define REN_PIN     33  // Right motor enable

// Buffers
#define MEAS_BUFSIZE 4  // Measurement buffer size
#define MSG_BUFSIZE 64  // Maximum length of an outgoing server message

// server address
IPAddress g_server_addr(192, 168, 1, 168);
uint16_t g_server_port = 3333;

// speed for both tracks
uint8_t g_speed = 180;

// controls whether the robot should take distance measurements
bool g_should_measure = false;

// map 4-bit values into various speed levels (in range 0 - 255)
uint8_t speed_map[16] = { 0, 0, 0, 130, 140, 150, 160, 170, 180, 190, 200, 210, 220, 230, 240, 250 };

AsyncUDP udp;

void setup()
{
  Serial.begin(115200);
  WiFi.mode(WIFI_STA);
  WiFi.begin(NETWORK_NAME, NETWORK_PASSWORD);
  if (WiFi.waitForConnectResult() != WL_CONNECTED) {
      Serial.println("WiFi Failed");
      while(1) {
          delay(1000);
      }
  }

  Serial.println("WiFi connected!");

  if(udp.connect(g_server_addr, g_server_port)) {
    Serial.println("UDP connected");
    //udp.print("Hello Server!");
    udp.onPacket([](AsyncUDPPacket packet) {
      // packet.data(), packet.length()

      //Serial.println("Packet received from server!");

      if (packet.length() == 0)
        return;

      // separate command key and value from the command byte
      uint8_t cmd_byte = packet.data()[0];
      uint8_t cmd_key = cmd_byte >> 4;
      uint8_t cmd_value = cmd_byte & 0b1111;

      // TODO: use handle table (interface?):
      // 0 => motorControl
      // 1 => speedControl
      // 2 => taskControl
      switch (cmd_key) {
        case 0:
          motorControl(cmd_value);
          break;
        case 1:
          speedControl(cmd_value);
          break;
        case 2:
          taskControl(cmd_value);
          break;
        default:
          break;
      }
    });

    // send a unicast message right after connecting
    udp.print("Hello Server!");
  }

  pinMode(BLINKER_PIN, OUTPUT);
  pinMode(LHALL_PIN, INPUT);
  pinMode(RHALL_PIN, INPUT);
  pinMode(UT_TRIG_PIN, OUTPUT);
  pinMode(UT_ECHO_PIN, INPUT);
  pinMode(L1_PIN, OUTPUT);
  pinMode(L2_PIN, OUTPUT);
  pinMode(LEN_PIN, OUTPUT);
  pinMode(R1_PIN, OUTPUT);
  pinMode(R2_PIN, OUTPUT);
  pinMode(REN_PIN, OUTPUT);
}

void loop()
{
  // TODO: Blink LED asynchronously
  //digitalWrite(BLINKER_PIN, HIGH);
  //delay(1000);
  //digitalWrite(BLINKER_PIN, LOW);
  //delay(1000);

  //uint16_t left_hall = analogRead(LHALL_PIN);
  //uint16_t right_hall = analogRead(RHALL_PIN);
  //Serial.print("left: ");
  //Serial.print(left_hall);
  //Serial.print(", right: ");
  //Serial.print(right_hall);
  //Serial.println();
  //delay(100);

#if 0
#define TEMPBUF_SZ 10

  uint16_t meas_buffer[TEMPBUF_SZ];

  for (int i = 0; i < TEMPBUF_SZ; i++) {
    meas_buffer[i] = analogRead(LHALL_PIN);
    delay(100);
  }

  AsyncUDPMessage msg_buffer(MSG_BUFSIZE);
  msg_buffer.printf("R_HALL: ");

  for (int i = 0; i < MEAS_BUFSIZE; i++) {
    msg_buffer.printf("%d", meas_buffer[i]);
    if (i < MSG_BUFSIZE)
      msg_buffer.printf(", ");
  }

  udp.sendTo(msg_buffer, g_server_addr, g_server_port);
  msg_buffer.flush();
  delay(100);
#endif

#if 0
  // take a series of measurements if tasked to do so
  if (g_should_measure) {
    long meas_buffer[MEAS_BUFSIZE];

    for (int i = 0; i < MEAS_BUFSIZE; i++) {
      meas_buffer[i] = measureDistance();
      delay(100);
    }

    AsyncUDPMessage msg_buffer(MSG_BUFSIZE);
    msg_buffer.printf("Distance measurements: ");

    for (int i = 0; i < MEAS_BUFSIZE; i++) {
      msg_buffer.printf("%ld cm", meas_buffer[i]);
      if (i < MSG_BUFSIZE)
        msg_buffer.printf(", ");
    }

    udp.sendTo(msg_buffer, g_server_addr, g_server_port);
    msg_buffer.flush();
    delay(100);
  }
#endif
}

// TODO: Add a small stop delay when changing directions!
/**
 * Left track forward.
 */
void leftTrackFW()
{
  digitalWrite(L1_PIN, HIGH);
  digitalWrite(L2_PIN, LOW);
  analogWrite(LEN_PIN, g_speed);
}

/**
 * Left track backward.
 */
void leftTrackBW()
{
  digitalWrite(L1_PIN, LOW);
  digitalWrite(L2_PIN, HIGH);
  analogWrite(LEN_PIN, g_speed);
}

/**
 * Left track stop.
 */
void leftTrackStop()
{
  digitalWrite(L1_PIN, LOW);
  digitalWrite(L2_PIN, LOW);
  analogWrite(LEN_PIN, 0);
}

/**
 * Right track forward.
 */
void rightTrackFW()
{
  digitalWrite(R1_PIN, HIGH);
  digitalWrite(R2_PIN, LOW);
  analogWrite(REN_PIN, g_speed);
}

/**
 * Right track backward.
 */
void rightTrackBW()
{
  digitalWrite(R1_PIN, LOW);
  digitalWrite(R2_PIN, HIGH);
  analogWrite(REN_PIN, g_speed);
}

/**
 * Right track stop.
 */
void rightTrackStop()
{
  digitalWrite(R1_PIN, LOW);
  digitalWrite(R2_PIN, LOW);
  analogWrite(REN_PIN, 0);
}

/**
 * Motor control.
 */
void motorControl(uint8_t cmd_byte)
{
  if (cmd_byte >= 16)
    return;

  //Serial.print("C> left track: ");
  switch ((cmd_byte & 0b1100) >> 2) {
    case 1:
      //Serial.print("forward");
      leftTrackFW();
      break;
    case 2:
      //Serial.print("backward");
      leftTrackBW();
      break;
    case 3:
      //Serial.print("stop");
      leftTrackStop();
      break;
    default:
      //Serial.print("[none]");
      break;
  }

  //Serial.print(", right track: ");
  switch ((cmd_byte & 0b0011) >> 0) {
    case 1:
      //Serial.print("forward");
      rightTrackFW();
      break;
    case 2:
      //Serial.print("backward");
      rightTrackBW();
      break;
    case 3:
      //Serial.print("stop");
      rightTrackStop();
      break;
    default:
      //Serial.print("[none]");
      break;
  }

    //Serial.println();
}

/**
 * Speed control.
 */
void speedControl(uint8_t speed_byte)
{
  if (speed_byte >= 16)
    return;

  g_speed = speed_map[speed_byte];
  //Serial.print("C> speed set to: ");
  //Serial.println(g_speed);
}

/**
 * Task control.
 */
void taskControl(uint8_t task_byte)
{
  if (task_byte >= 16)
    return;

  g_should_measure = task_byte == 1;
  //Serial.print("C> measurement control set to: ");
  //Serial.println(g_should_measure ? 'active' : 'inactive');
}

//void sendMessage(std::string message)
//{
//  AsyncUDPMessage msg_buffer(MSG_BUFSIZE);
//
//  msg_buffer.printf("Counter value: %d", counter);
//  udp.sendTo(msg_buffer, g_server_addr, g_server_port);
//}
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

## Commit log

2023-03-14 Working motor demo for ESP32
2023-03-14 Added UDP receiver which can now receive messages from ESP32
2023-03-14 UDP packets now flow to both directions
2023-04-19 Finally control motors from the server
2023-04-24 Added ultrasonic sensor, some refactoring
2023-06-01 UT measurement, control flows and more
2023-09-24 Track robot angle - very WIP
2024-04-13 Started major cleanup and refactoring
    [Mobrob.kicad_pcb, Mobrob.sch, mobrob-v1.kicad_pcb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]
2024-04-15 Sketching the schematic
    [mobrob.kicad_pcb, mobrob.sch]
2024-06-16 Massive dump
    [Mobrob.sch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]
2024-06-21 Added sample credentials file
2024-06-26 Started work on sensors - UT done
2024-06-26 IMU sensor done
2024-06-26 Removed old HW project
    [mobrob.kicad_pcb, mobrob.sch]
2024-06-26 Started test development for robot - Motor and Drive done
2024-06-27 Removed backyard
    [Mobrob.kicad_pcb, Mobrob.sch, mobrob-v1.kicad_pcb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]
